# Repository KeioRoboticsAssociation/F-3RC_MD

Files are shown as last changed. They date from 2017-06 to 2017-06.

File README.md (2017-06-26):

# モータドライバ（SN754410NE）基板

[SN754410NEのデータシート](http://akizukidenshi.com/download/ds/ti/SN754410NE.pdf)

## この基板を設計した経緯

モータードライバは壊れやすい。そのたびにユニバーサル基板で作りなおすと
結構キツい。それに大会間近に故障で試験走行ができない時間ができると
超もったいない。どうせ同じものを複数個作るなら、プリント基板でキット化して、
ドライバ故障→交換までのストレスを減らそう！ってこと。それだけ。
　一応、1年生が参加することになってるF^RC用に使うことを考えて始めた計画だけど、
あとに書くスペックを見て、自分の要求を満たしているならなんでも使えると思う。

## 仕様

詳しいことはデータシートを読んだ方がいいと思うので、使う上で必要そうなこと
だけをまとめておく。

| 場所 | 特性 |
|---|---|
| ロジック電源 | 4.5〜5.5V（2.1mｍ標準DCコネクタ） |
| モーター電源 | 4.5〜36V（2.1mｍ標準DCコネクタ） |
| 出力 | ピンヘッダ or ピンソケット1x8 |
| 入力 | デジタル入力・PWM（High=2〜5.5V、Low=-0.3〜0.8V、ピンソケット） |

ICひとつにハーフブリッジ回路が４つ入っている。モーターを正転・逆転させたい、
またはブレーキをかけたい場合はICひとつでモーター2個駆動できる。また、モーターを
一方向にしか回さない、かつブレーキはいらない場合はICひとつで
モーター4個駆動できる。ここで注意してほしいのは、
「ブレーキがかけられない≠止まらない」だということ
（モーターの電源を切ればしばらく走って止まる）。

INPUTピンの番号は、左(DCコネクタがある方)から順にA1, A2, A3, A4, A1, A2, A3, A4
になっている。同様にOUTPUTピンの番号はY1, Y2, Y3, Y4, Y1, Y2, Y3, Y4になっている。
AピンとYピンは1対1対応してる。入力AがHighなら向かい合う出力YもHigh。
Lowの場合も同じ。詳しくはデータシートの図を見てほしい。

ちなみにENピンはICに含まれる回路の半分だけ電源を切りたいときとかに使える
ようだが、このプリント基板では常にHighになるよう設計されている。

## 部品表

| 番号（基板に書いてある） | 部品名（秋月のホームページとかで調べて） | 個数 | 備考 |
|---|---|---|---|
| P1, P2 | 基板取り付け用DCジャック | 2 | センタープラス（中心の棒プラス）だよ。 |
| P3, P4 | ピンヘッダ or ピンソケット1x8 | 2 | 挿す方でも挿される方でもご自由に。 |
| C1, C3 | 電解コンデンサ(100μF 35V) | 2 | 直径6.3mm以上のコンデンサだと周りの部品に干渉するかも。足の長い方がプラスに繋がる。 |
| C2, C4 | 積層セラミックコンデンサ(0.4μF 50V) | 2 | |
| U1, U2 | モータードライバIC（SN754410NE） | 2 | 実際はんだ付けするのはICソケット（16P）にした方がいいよ。 |

## 外観

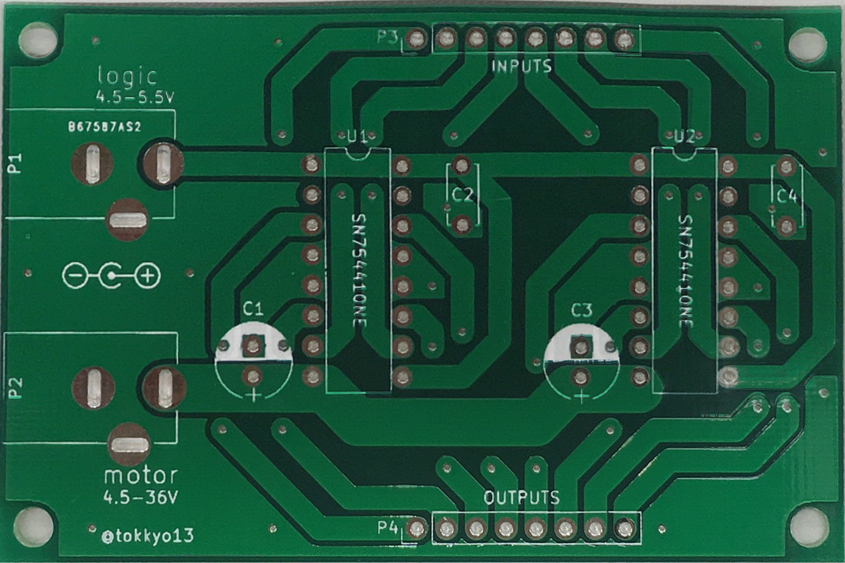
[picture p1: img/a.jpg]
未実装


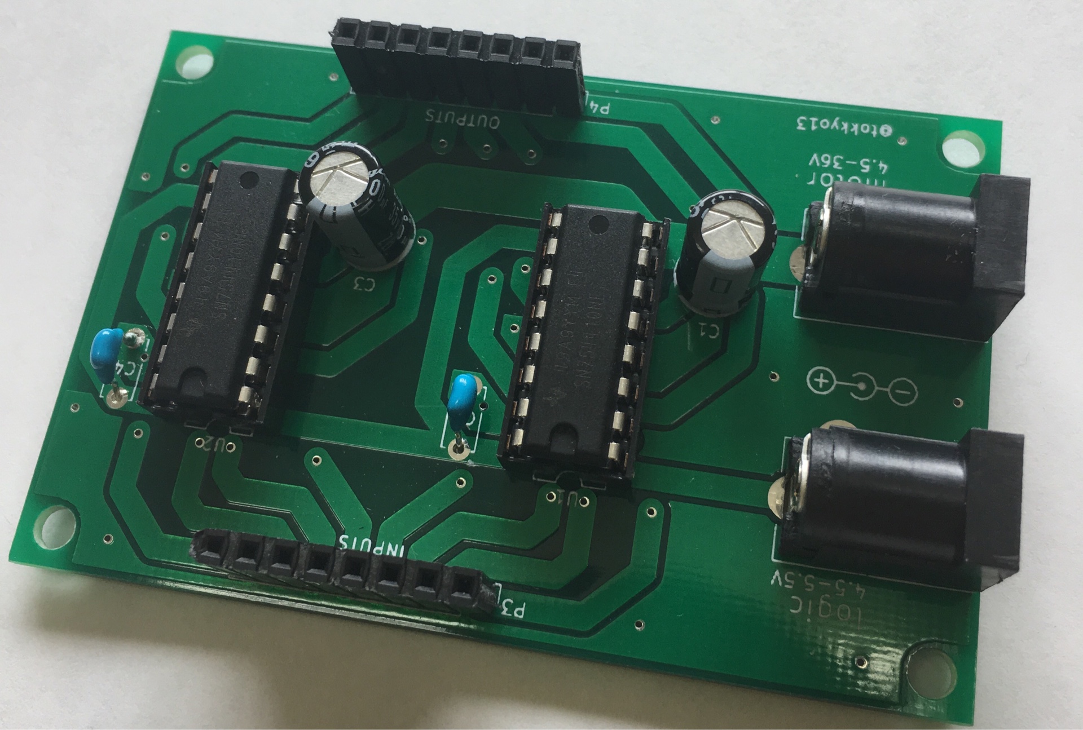
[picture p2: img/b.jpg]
実装済


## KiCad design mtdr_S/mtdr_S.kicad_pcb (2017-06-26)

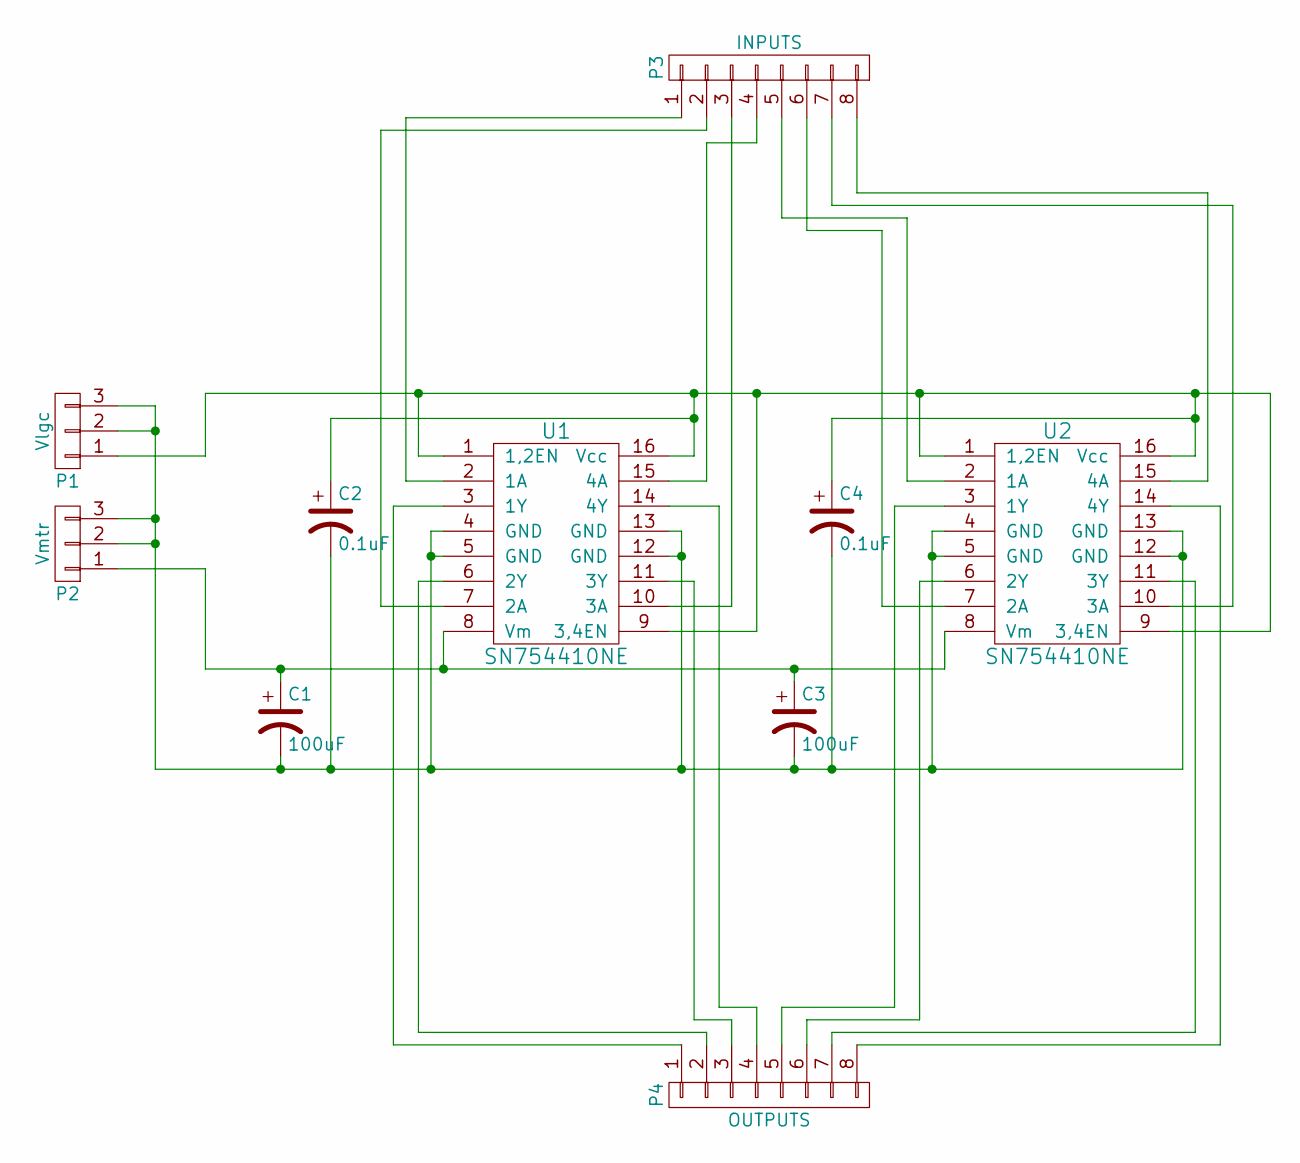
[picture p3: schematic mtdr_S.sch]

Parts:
C1, C3: 100uF; CP_Radial_D6.3mm_P2.50mm
C2, C4: 0.1uF; C_Disc_D5.0mm_W2.5mm_P5.00mm
P1: Vlgc; BARREL_JACK
P2: Vmtr; BARREL_JACK
P3: INPUTS; Pin_Header_Straight_1x08_Pitch2.54mm
P4: OUTPUTS; Pin_Header_Straight_1x08_Pitch2.54mm
U1, U2: SN754410NE; DIP-16_W7.62mm

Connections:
unnamed: C1.1, C3.1, P2.1, U1.8 (Vm), U2.8 (Vm)
unnamed: C1.2, C2.2, C3.2, C4.2, P1.2, P1.3, P2.2, P2.3, U1.4 (GND), U1.5 (GND), U1.12 (GND), U1.13 (GND), U2.4 (GND), U2.5 (GND), U2.12 (GND), U2.13 (GND)
unnamed: C2.1, C4.1, P1.1, U1.1 (1,2EN), U1.9 (3,4EN), U1.16 (Vcc), U2.1 (1,2EN), U2.9 (3,4EN), U2.16 (Vcc)
unnamed: P3.1, U1.2 (1A)
unnamed: P3.2, U1.7 (2A)
unnamed: P3.3, U1.10 (3A)
unnamed: P3.4, U1.15 (4A)
unnamed: P3.5, U2.2 (1A)
unnamed: P3.6, U2.7 (2A)
unnamed: P3.7, U2.10 (3A)
unnamed: P3.8, U2.15 (4A)
unnamed: P4.1, U1.3 (1Y)
unnamed: P4.2, U1.6 (2Y)
unnamed: P4.3, U1.11 (3Y)
unnamed: P4.4, U1.14 (4Y)
unnamed: P4.5, U2.3 (1Y)
unnamed: P4.6, U2.6 (2Y)
unnamed: P4.7, U2.11 (3Y)
unnamed: P4.8, U2.14 (4Y)

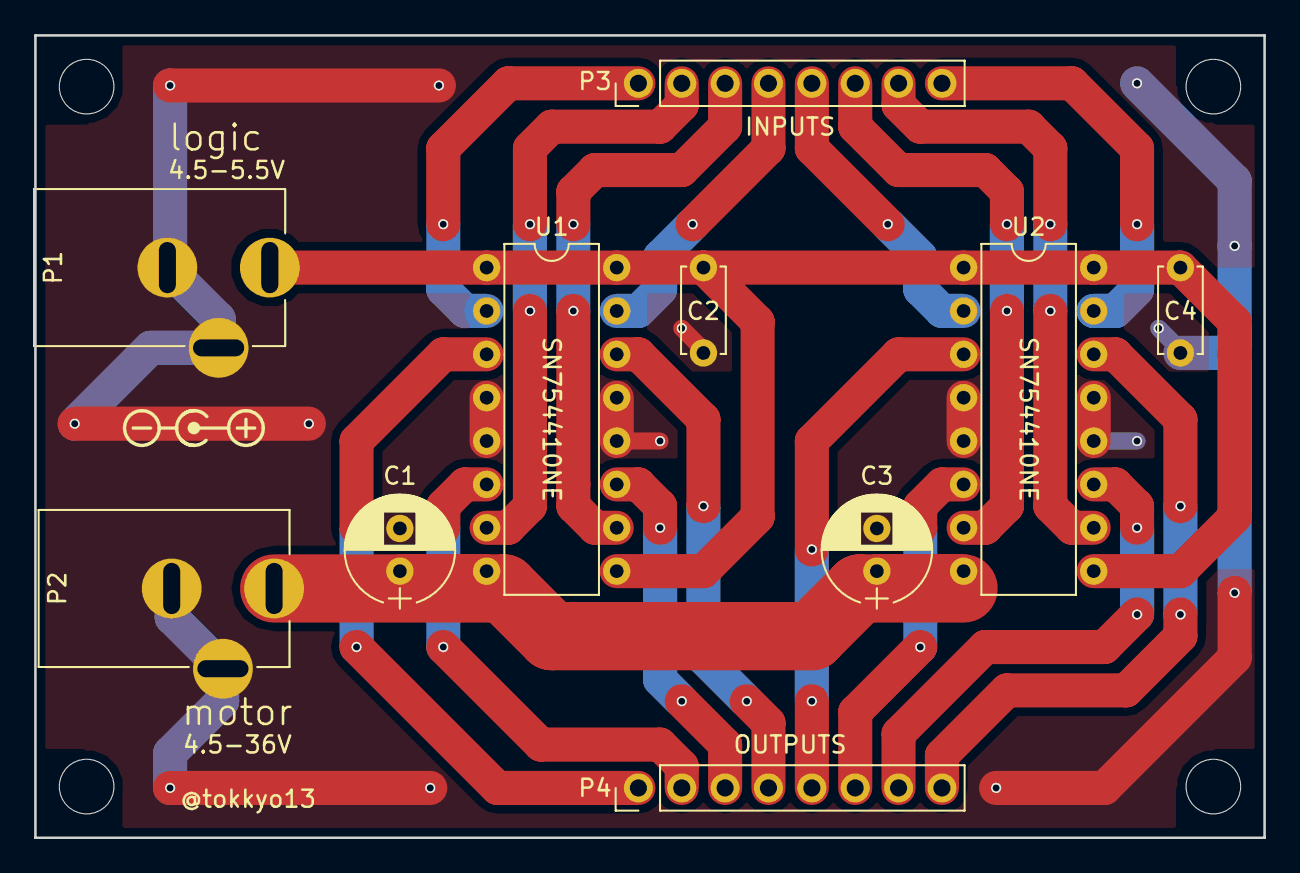
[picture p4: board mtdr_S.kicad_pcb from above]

Board: 2 copper layers, 72.0 x 47.0 mm, 10 parts (0 on the bottom side), 19 nets.

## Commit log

2017-06-19 説明書に少し変更を加えた
2017-06-19 余計なファイル消した
2017-06-26 schを追加
    [mtdr_S.sch]
2017-06-26 add relevant files
    [mtdr_S.kicad_pcb, mtdr_S.sch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]
